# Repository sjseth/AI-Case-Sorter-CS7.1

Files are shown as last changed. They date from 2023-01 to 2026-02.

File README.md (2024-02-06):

# AI-Case-Sorter-CS7.1

This is a project for building a case sorter which uses machine vision, machine learing AI to sort cases by headstamp. This repo contains the Arduino code as well as all the 3d Models required to complete this project. 

## Instructions
Most of the information you need to build this project is available in [Instructions.pdf](Instructions.pdf).

---------
## Parts List
The parts list for this project can be found here:
[Parts List](https://www.reloadingrecipes.com/HeadstampSorter/Partslist)

--------

# CS7.1 Video Build Series

The release video for this project is here:

Watch the video (https://youtu.be/s7dy0odA44U)

Follow along with me as I build the various components of this system. 

## Classifier
Build the Classifier (https://youtu.be/lhxDmvg5AVQ)

## Sorter
Build the Sorter (https://youtu.be/rP7bBV_uqF4)

## Camera Module
Build the Camera (https://youtu.be/iOc7inAcXpQ)

## Electronics
Build the Electronics (https://youtu.be/cS54LOCpNGc)

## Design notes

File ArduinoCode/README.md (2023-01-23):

# AI-Case-Sorter-CS7.1
This repo was created to isolate all the code and resources for the CS7.1 Version

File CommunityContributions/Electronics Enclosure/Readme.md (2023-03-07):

# This is the place where you can put your Electronics Enclosure contributions to the project for cs7.1

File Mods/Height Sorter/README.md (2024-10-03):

# Height Sorter Mod

This mod is was designed by user JK and made to sort brass by height which is usefull for seperating 223 from 300 BLK or 9mm from 380, etc. 

It requires seperate arduino code (in this folder) and leverages a different classifier base design as well as a taller tension cam. 

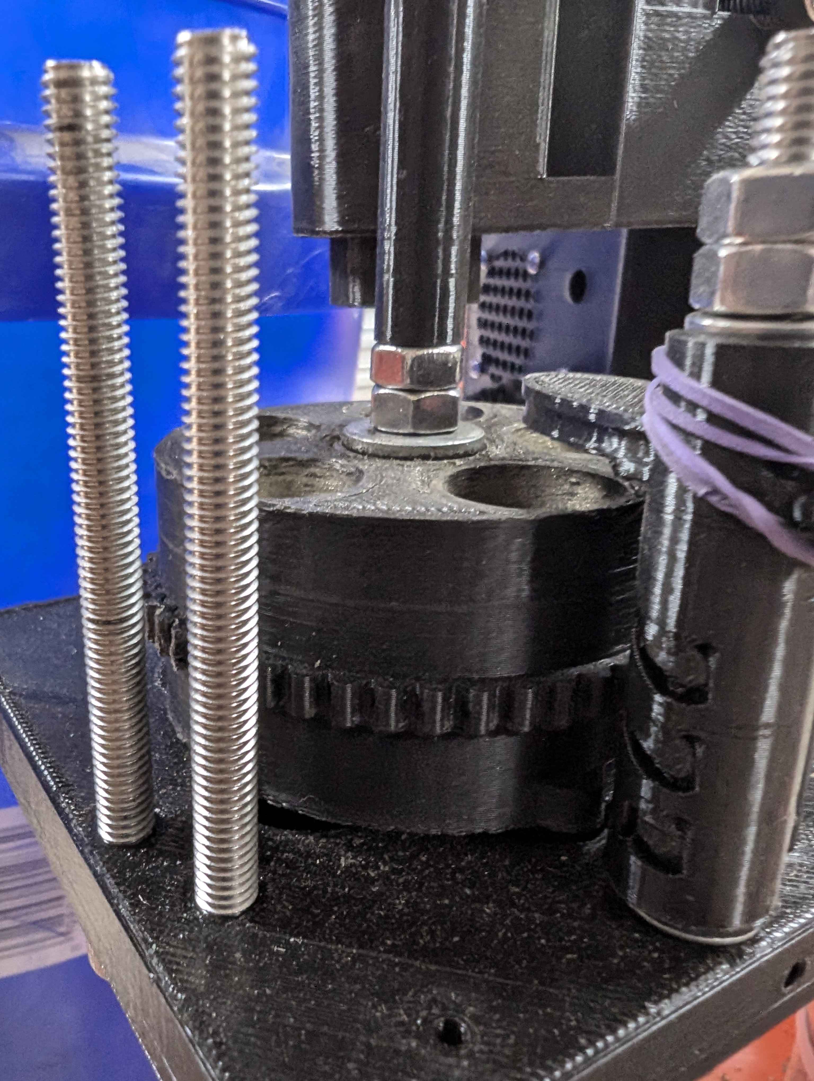
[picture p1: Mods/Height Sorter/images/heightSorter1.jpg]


<i> More details coming soon! </i>

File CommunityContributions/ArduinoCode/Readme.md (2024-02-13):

# Community Contributions for Arduino Code

### Index

* Sabre1911 - SKR PICO Support

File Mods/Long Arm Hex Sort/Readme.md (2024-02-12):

# Long Arm Hex Sort

These resources were created for those who would like to have more slots than the standard 8 provided.  By extending the arm length, we swing in a wider radius thus creating more room for buckets or containers. To make this possible, I had to change the geometry of the sort tube to have a hexagon outer contour which allows it to be printed on its side. This also has the effect of aligning the print lines with the direction the brass flows so it provides improved drop performance.

To get started, you need to print all 3 resources

[Hex Pipe Bracket](CS7.1%20-%20LAHS%20-%20Pipe%20Bracket.stl)

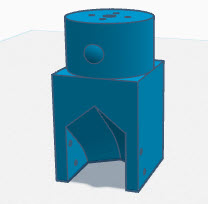
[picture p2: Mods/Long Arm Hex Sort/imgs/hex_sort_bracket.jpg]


[Hex Pipe 200mm Length](CS7.1%20-%20LAHS%20-%20HexPipe%20-%20200mm.stl)

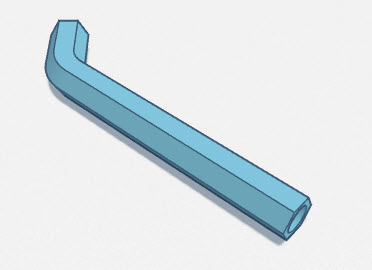
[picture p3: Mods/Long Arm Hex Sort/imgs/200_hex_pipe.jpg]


[Homing Bracket](CS7.1%20-%20LAHS%20-%20Homing%20Bracket.stl)

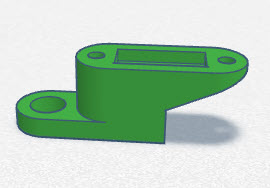
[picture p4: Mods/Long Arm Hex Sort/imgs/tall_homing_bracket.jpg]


Here is a short video of what it will look like

Video Example (https://youtu.be/aqpXGkVaJ-k)

Additionally, you will need to make some configuration updates in the AI Sorter software. 
- Set **Sort Motor Speed** to 80  (or slower)
- Set **Slot Drop Delay** to 600 (if not, the brass wont clear the tube before move)
- Set the **Slot Step Increment** to 15
- Increase the **Slot Count** to 11.

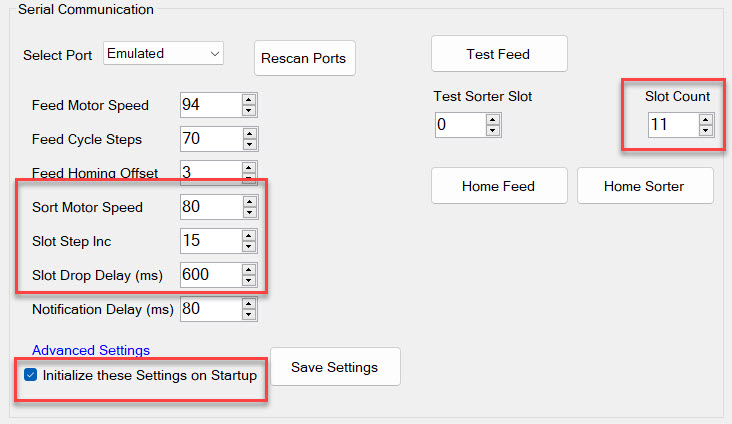
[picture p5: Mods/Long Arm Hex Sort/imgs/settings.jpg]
Settings
]

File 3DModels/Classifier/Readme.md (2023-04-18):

# Classifier Models

The parts in this folder represent everything that is needed to build the classifier. You will need to print at least one of the caliber specific feed wheels and nozzles as well. 

In the release video, there were a few add-ons which can be found in the Community Folder at the top/root folder in the repo. Those items are linked here as well:

## [Quick Change Light Shade and Locking System](https://github.com/sjseth/AI-Case-Sorter-CS7.1/tree/main/CommunityContributions/Classifier/Karl)

## [AirDrop System](https://github.com/sjseth/AI-Case-Sorter-CS7.1/tree/main/CommunityContributions/Classifier/SJSETH)

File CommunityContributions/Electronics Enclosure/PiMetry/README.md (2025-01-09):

# PiMetry

## Spacious Electronics Enclosure

Enclosure with more space for hassle free cable management with two fan slots.
The enclosure is made for the software dimmer mod, if you want to use the physical dimmer you need to modify the case or drill a hole for it.

[Pole mount from shibby](../Shibby/CS7.1a_-_Electronics_Box_Mount_1inch.stl)

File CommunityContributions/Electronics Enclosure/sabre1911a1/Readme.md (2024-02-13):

These STLs were designed to work with the BTT SKR Pico board. They will not work with the Arduino electronics.

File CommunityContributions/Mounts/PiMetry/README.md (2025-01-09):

# PiMetry

## 2020 Mounts

These mounts are intended to be used with m4 t slot nuts and bolts.
There are many 3d printable connectors for aluminum extrusions available on the usual STL / STEP file collection sites which might come in handy.

### 2020OffsetMount

Allows mounting a 2020 extrusion aside another horizontal 2020 extrusion.

### 2020OffsetTubeMount

Allows mounting a 25mm tube aside another horizontal 2020 extrusion.

### 2020TubeMount

Allows mounting a 25mm tube on top of another horizontal 2020 extrusion.

### 2020VesaMount-TwoScrew

Allows mounting a screen with two VESA bolts to a vertical 2020 extrusion.

### Electronics Enclosure Mount

Allows mounting the electronics enclosure to a vertical 2020 extrusion.

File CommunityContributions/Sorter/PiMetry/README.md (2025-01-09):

# PiMetry

## Dust Collector Hose Sorter (6 Slot)

This 6 Slot Sorter is intended for transparent and flexible PVC 50mm ID hoses with a coiled wire.
Tested with 9mm and 308 Win cases.
2 inch hoses should work as well.

Thicker or very stiff hoses are not recommended.

The hoses are connected using eg. 40 - 60 mm hose clamps
Couplers use 5x4mm round magnets (5 diameter, 4 height)

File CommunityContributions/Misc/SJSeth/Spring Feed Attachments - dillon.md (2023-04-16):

# Dillon spring feed tube adaptor

This adaptor is for a 15mm OD spring and can be attached to both ends of the spring as it fits in the dillon collator clips as well as the AI Sorter feed tubes. 

Recommend printing it with brim of at least 6 lines for better adhesion. 

[1x15x1000 Spring](https://www.aliexpress.us/item/2251832626574002.html)

This spring took about 2 weeks to get to the US and comes with two 1000mm springs Which is enough to make aproximately 6 - 8 feed tubes. 

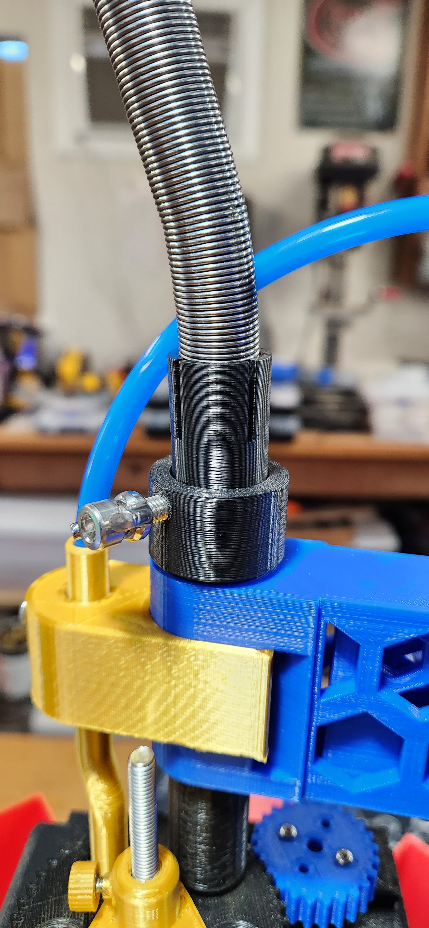
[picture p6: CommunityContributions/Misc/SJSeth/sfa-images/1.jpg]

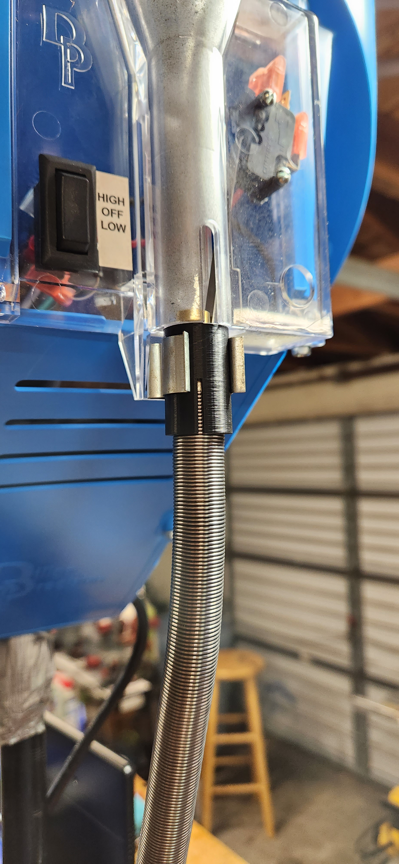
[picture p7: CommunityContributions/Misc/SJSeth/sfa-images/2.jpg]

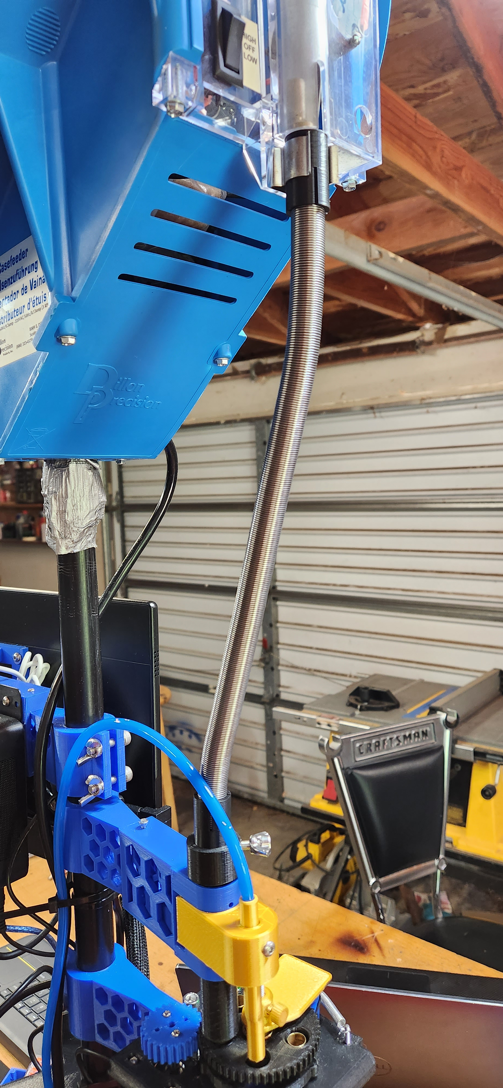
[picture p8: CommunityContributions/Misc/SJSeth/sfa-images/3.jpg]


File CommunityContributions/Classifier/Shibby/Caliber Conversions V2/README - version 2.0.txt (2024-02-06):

CS7.1 Caliber Conversions enhanced by Shibby - v2.0 - 11/20/23

Summary of changes from stock CS7.1 conversions

Conversions with "S" (i.e CS7.1s) - resized bearing hole to "19.0" and caliber designations. WARNING -Super tight fit. 
Conversions with "A" (i.e CS7.1a) - resized bearing hole to "19.2" and caliber designations. WARNING - This is a press fit. 
Conversions with "E" (i.e CS7.1e) - Stock bearing hole "19.6" just with caliber designations. Will behave as the standard CS7.1 conversions. 

Summary of changes since initial release (non version designated readme file)- 

Added "s" versions of conversions.

On the wheels, the cal designation will be on the top of the unit. Tubes have a circle sunk into them with designations popping out a touch.

Tubes are all caliber labeled with no letter designation in the naming scheme. Treat them as you would the normal files. 

Tube Varient - Keyed for BF556 feeder adaptors

45GAP conversion created for all 3 people in the world who shoot it. Use 45acp feed tubes with it. Useful for sorting 45GAP from 45ACP in one wheel. Consider interchangeable with standard 45acp wheel. 

These work for me and I make no guarantee they work for you.

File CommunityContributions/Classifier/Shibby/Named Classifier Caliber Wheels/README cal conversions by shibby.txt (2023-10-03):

CS7.1 Caliber Conversions enhanced by Shibby

Summary of changes from stock CS7.1 conversions

Conversions with "a" (i.e CS7.1a) - resized bearing hole to "19.2" and caliber designations. WARNING - This is a press fit so it may or may not work for you depending on how you have dialed in the printer you are using and the bearings you are using. 

Conversions with "E" (i.e CS7.1E) - Stock bearing hole "19.6" just with caliber designations. Will behave as the standard CS7.1 conversions. 

These work for me and I make no guarantee they work for you.

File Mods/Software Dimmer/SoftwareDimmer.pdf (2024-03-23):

# CS7.1 Software Light Dimmer Mod

### Overview

This mod replaces the hardware based light dimmer knob in the electronics box with a software-controlled system. Arduino supports PWM (pulse width modulation) signals which can be relayed through a pwm switch. In this mod, we are using the same MOSFET relay switch which is used for the AirDrop mod .

### Hardware Required

The only additional hardware required for this mod is the MOSFET pwm switch/relay which is the same one we use for the Airdrop mod.

https://amzn.to/3Ac9f7Y

### Installation

Unfortunately, not all pins are supported on the Arduino for PWM signals so we need to “trade” one of the currently used pins which supports PWM for one that doesn’t. On the Arduino Shield, pin D13 (labeled SpnDir) will become the new pin for proximity sensor (currently X+ or D9) and we will use the X+ pin for the PWM dimmer signal.

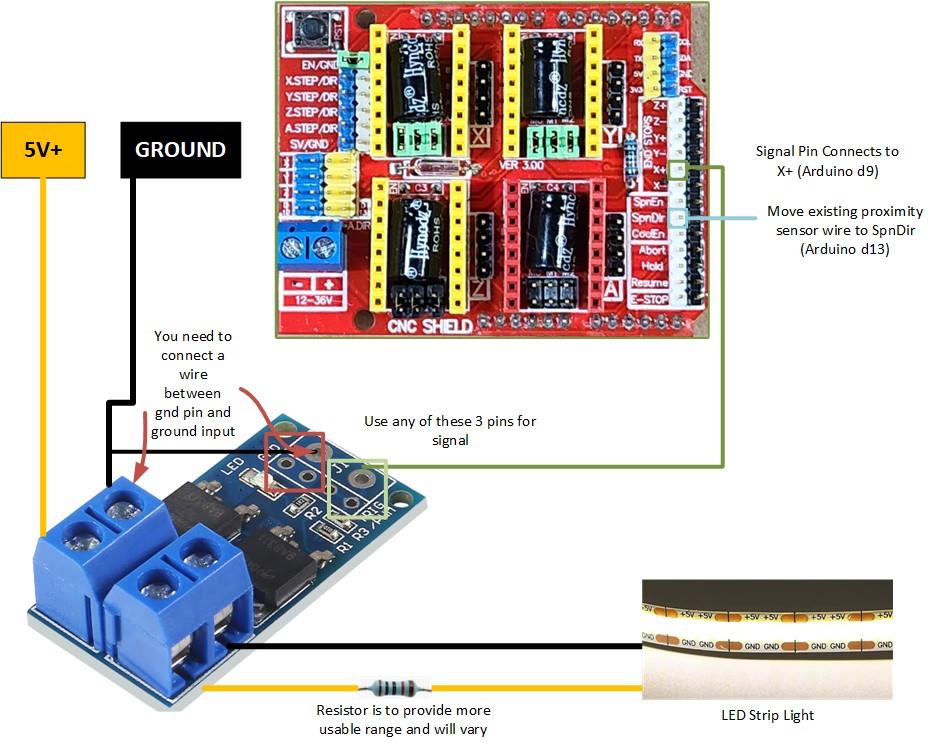
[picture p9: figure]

### Inline Resistor

The inline resistor as seen in the screenshot above is not required but can help to provide a better range of light depending on your setup. For instance, if you are using clear PLA in your light ring, you may want to add a 1k resistor. For a white PLA light ring, a value closer to 200 ohm may be more appropriate. It is recommended to try it without a resistor first and see if you are able to get the right amount of light while still having range to adjust up or down. The range of the dimmer control is 0-255.

### Configuring the Arduino

Finally, you need to make two changes in the Arduino code to enable and use this feature.

The first parameter you need to change is named UseArduinoPWMDimmer and the value needs to be set to true as seen in the screenshot below.

The second value you can change is the default light brightness value. Note that once you enable this mod, you will have an option to adjust this value in the software, so it is fine to leave the value as set.

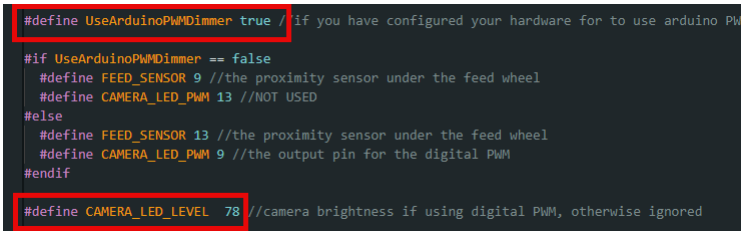
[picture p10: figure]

Once you have updated the code, you need to upload it to your Arduino. When that is complete, close the Arduino IDE and launch the software (v1.1.45 or later)

You will now see an option in the software to adjust the light brightness in the Configuration panel. It is best to hit the “Preview” button to turn on the camera and then adjust the slider until you achieve the appropriate brightness.

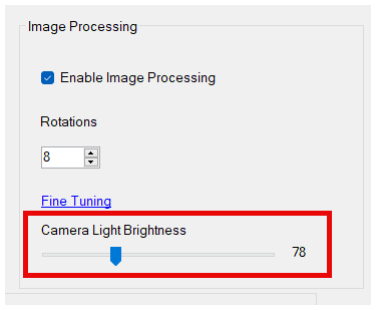
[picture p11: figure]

Be sure to save your configuration changes once you have adjusted this setting.

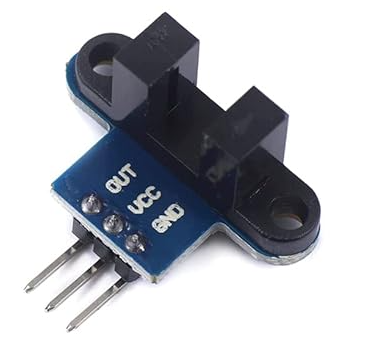
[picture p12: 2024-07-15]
CommunityContributions/Classifier/SJSETH/Optical_Homing_Sensor/imgs/sensor_amz.png

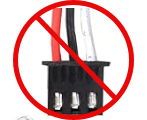
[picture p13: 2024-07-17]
CommunityContributions/Classifier/SJSETH/Optical_Homing_Sensor/imgs/sensorwire2.png

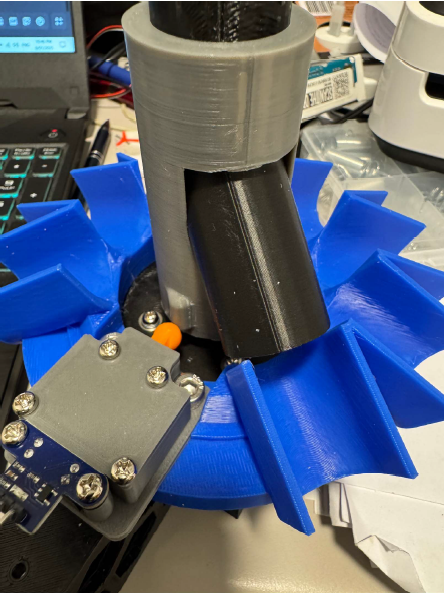
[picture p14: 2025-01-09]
CommunityContributions/Sorter/Mullet/Optical Sorter Switch/images/image.png

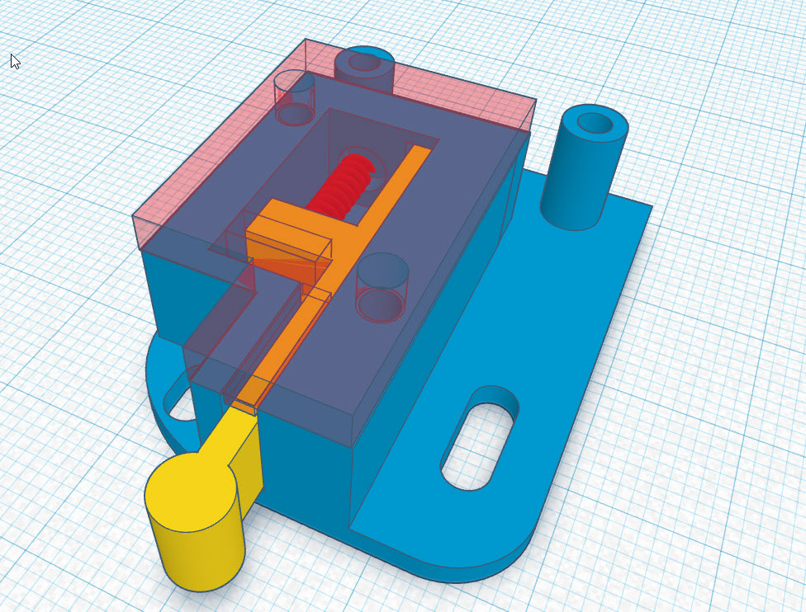
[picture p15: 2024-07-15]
CommunityContributions/Classifier/SJSETH/Optical_Homing_Sensor/imgs/sensor3d.jpg

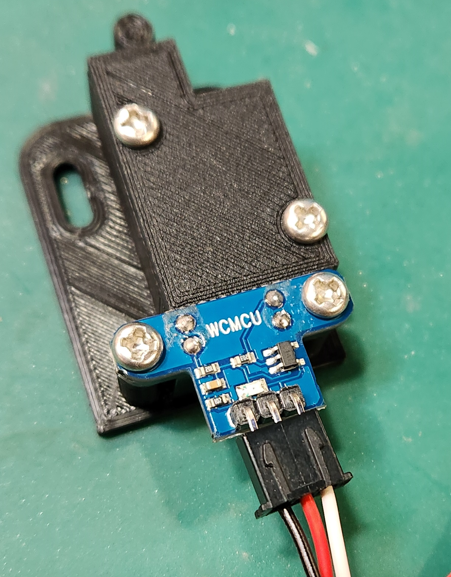
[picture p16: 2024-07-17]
CommunityContributions/Classifier/SJSETH/Optical_Homing_Sensor/imgs/sensorwire1.png

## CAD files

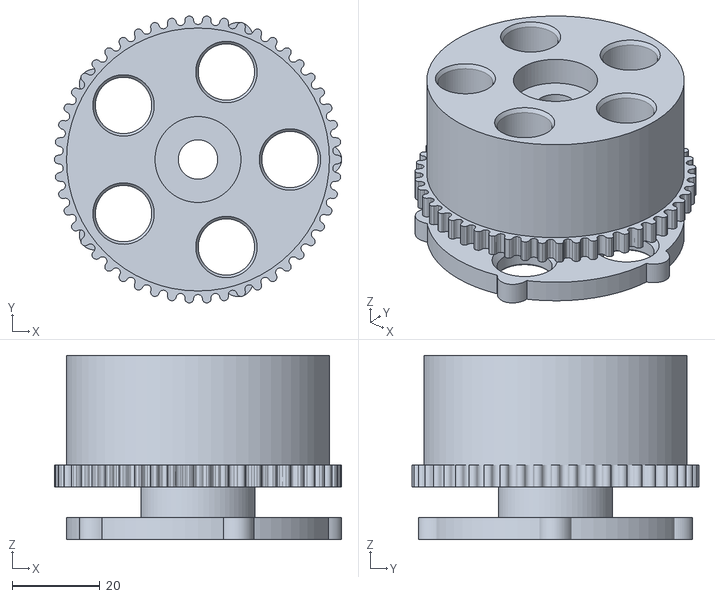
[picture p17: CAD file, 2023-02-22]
3DModels/Classifier/Caliber Specific Parts/223_556/CS7.1 223_556 Feed Wheel.stl
65.6 x 65.5 x 42.0

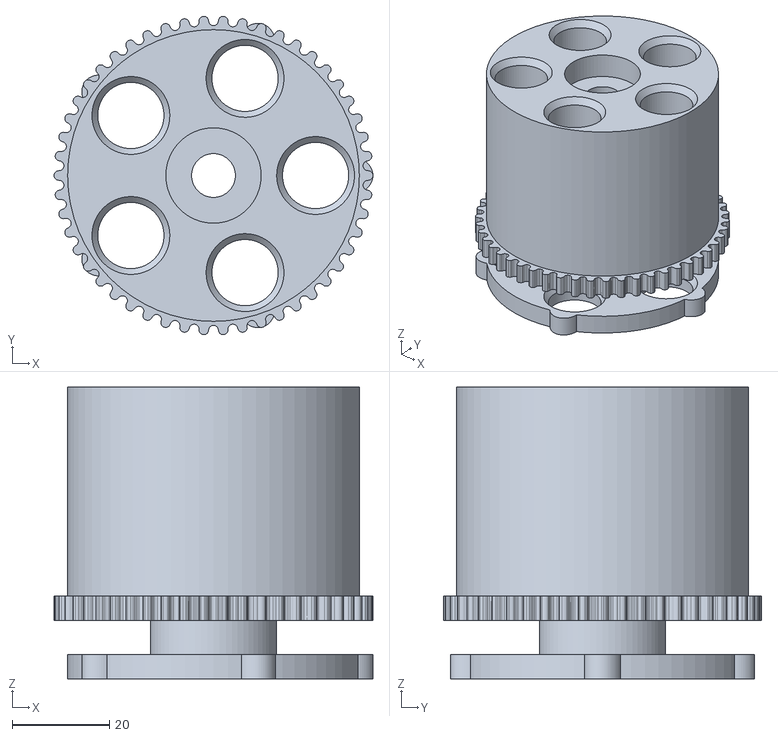
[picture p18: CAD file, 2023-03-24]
3DModels/Classifier/Caliber Specific Parts/30-06_270/CS7.1 30.06 Feed Wheel.stl
65.6 x 65.5 x 60.0

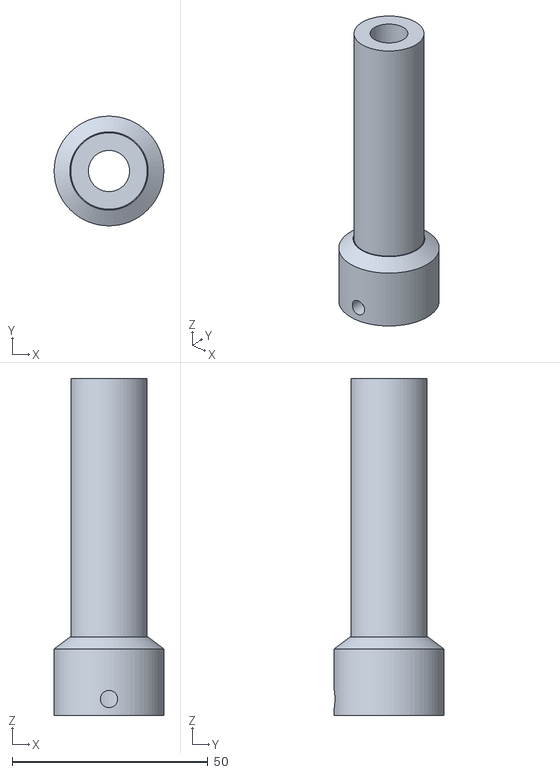
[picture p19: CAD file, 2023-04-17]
3DModels/Classifier/Caliber Specific Parts/300_Blackout/CS7.1 300 Blackout Feed Nozzle.stl
28.0 x 28.0 x 86.0

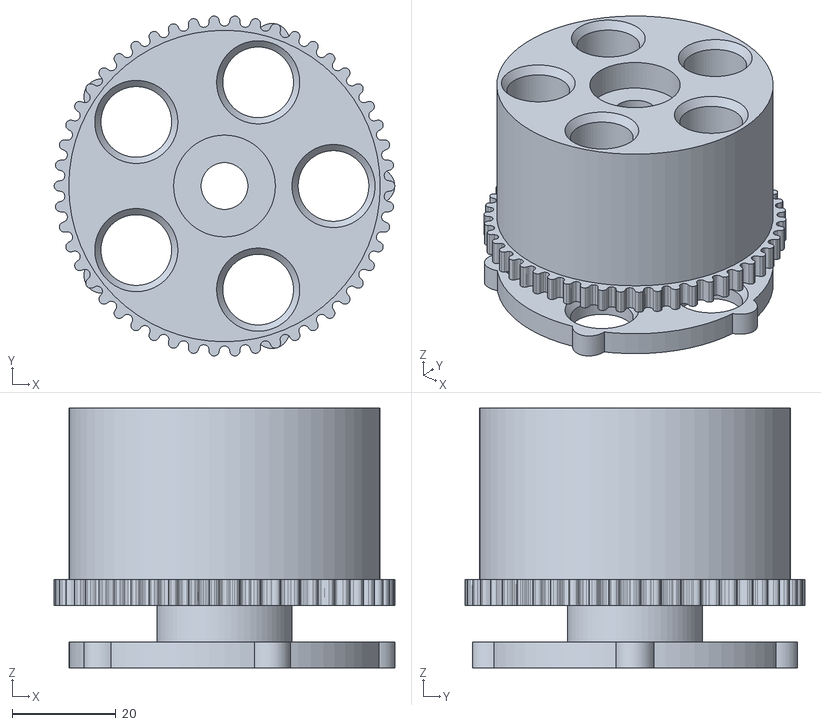
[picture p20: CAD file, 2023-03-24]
3DModels/Classifier/Caliber Specific Parts/308win/CS7.1 308Win Feed Wheel.stl
65.6 x 65.5 x 50.0

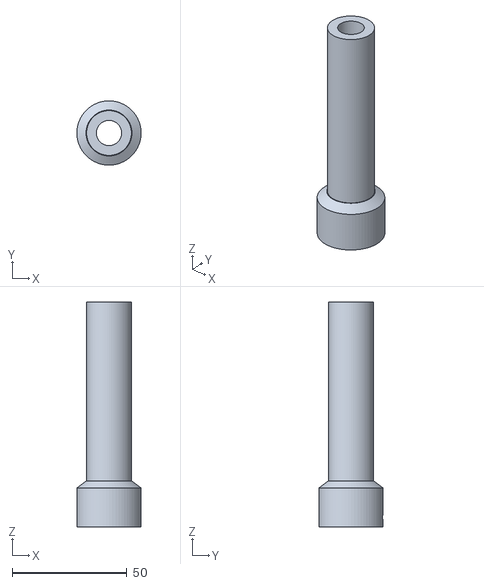
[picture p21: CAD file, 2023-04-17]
3DModels/Classifier/Caliber Specific Parts/32SWLong/CS7.1 32SWLong Feed Nozzle.stl
28.0 x 28.0 x 98.0

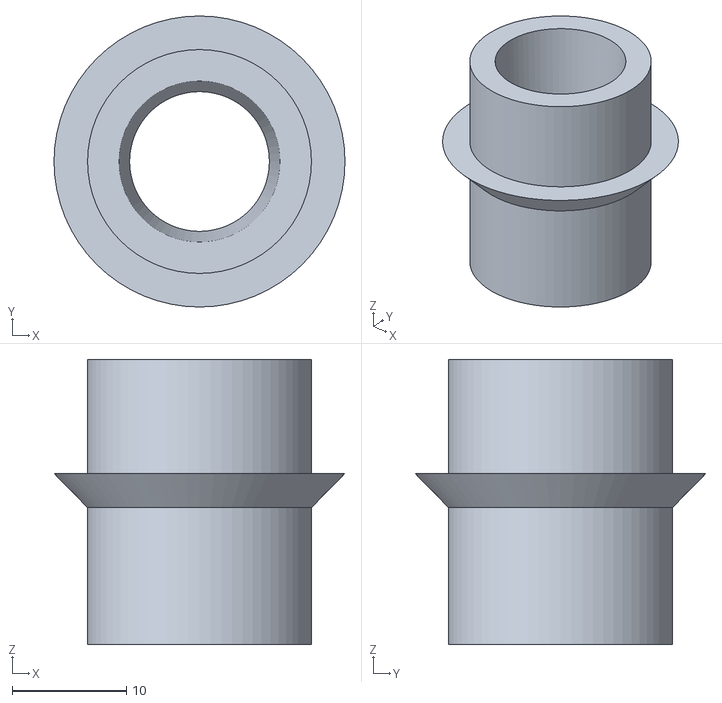
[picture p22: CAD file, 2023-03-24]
3DModels/Classifier/Caliber Specific Parts/38_Special/CS7.1 38 Special Drop Nozzle.stl
25.5 x 25.5 x 25.0

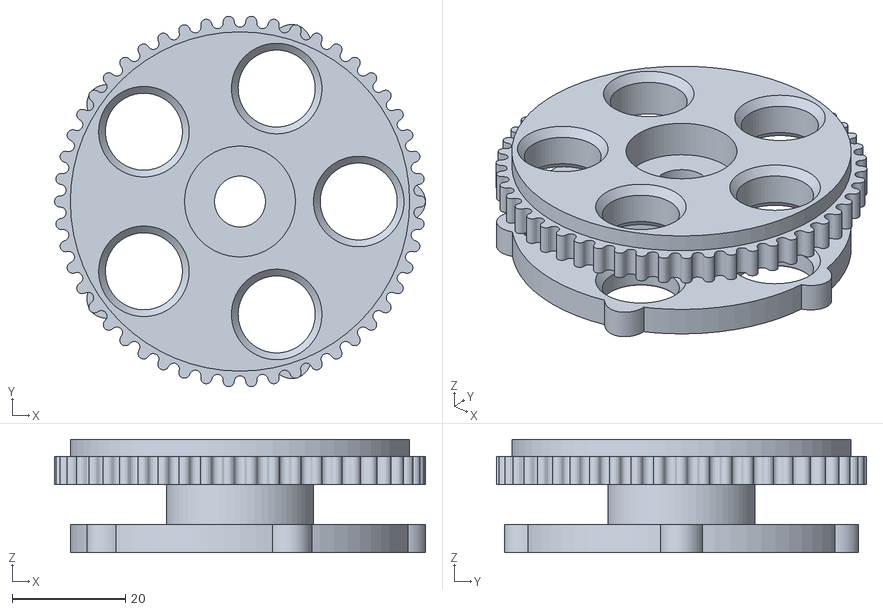
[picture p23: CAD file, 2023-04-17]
3DModels/Classifier/Caliber Specific Parts/40SW/CS7.1 40SW Feed Wheel.stl
65.6 x 65.5 x 20.0

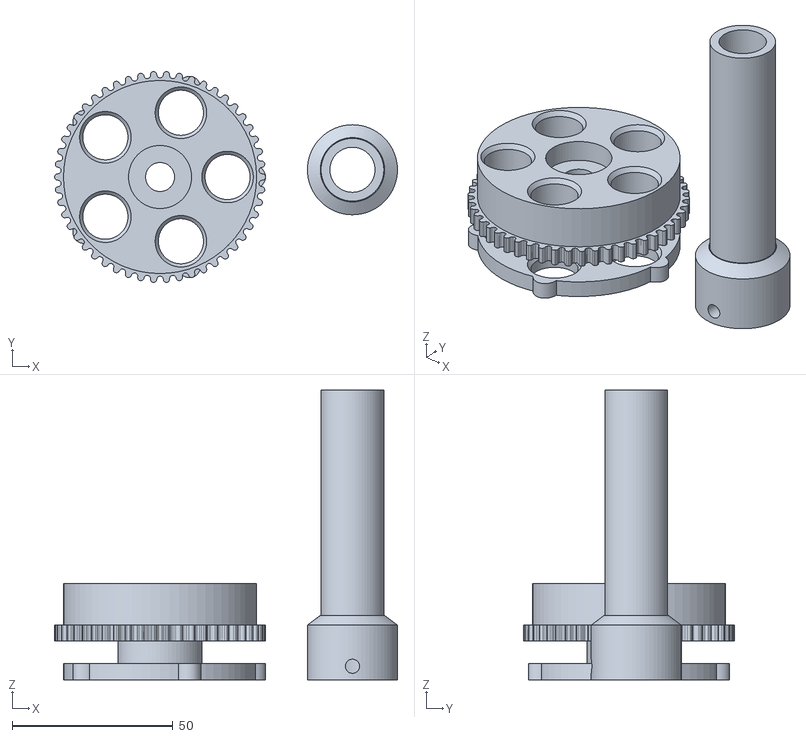
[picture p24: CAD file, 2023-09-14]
3DModels/Classifier/Caliber Specific Parts/45Colt_44Mag/CS7.1 Caliber Conversion 45Colt_44Mag.stl
106.6 x 65.5 x 90.0

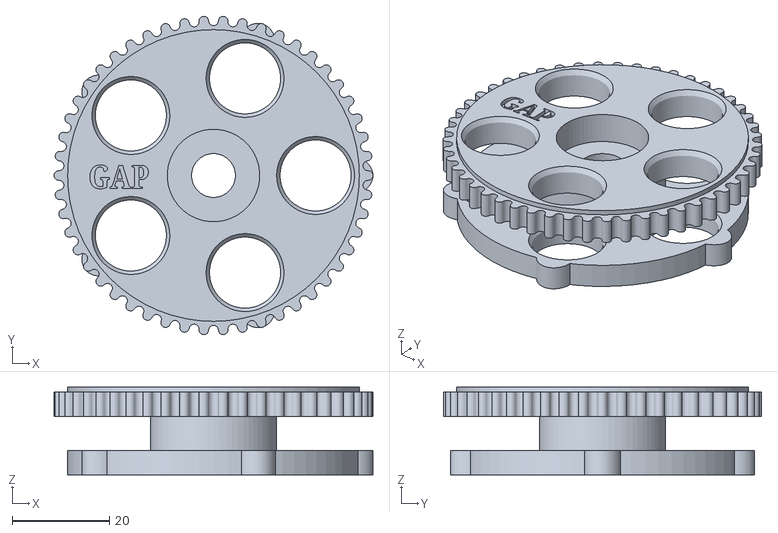
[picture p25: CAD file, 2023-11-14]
3DModels/Classifier/Caliber Specific Parts/45GAP/CS7.1e_Caliber_Conversion_45gap.stl
65.6 x 65.5 x 18.0

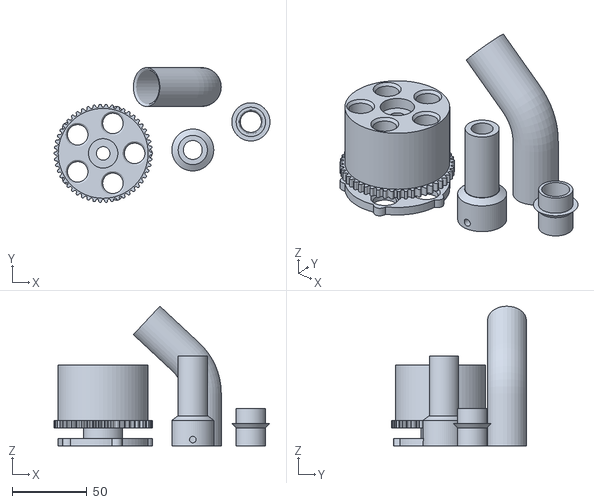
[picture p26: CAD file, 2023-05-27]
3DModels/Classifier/Caliber Specific Parts/7.92x57_Mauser/CS7.1 Caliber Conversion 7.92x57M.stl
144.1 x 90.0 x 93.2

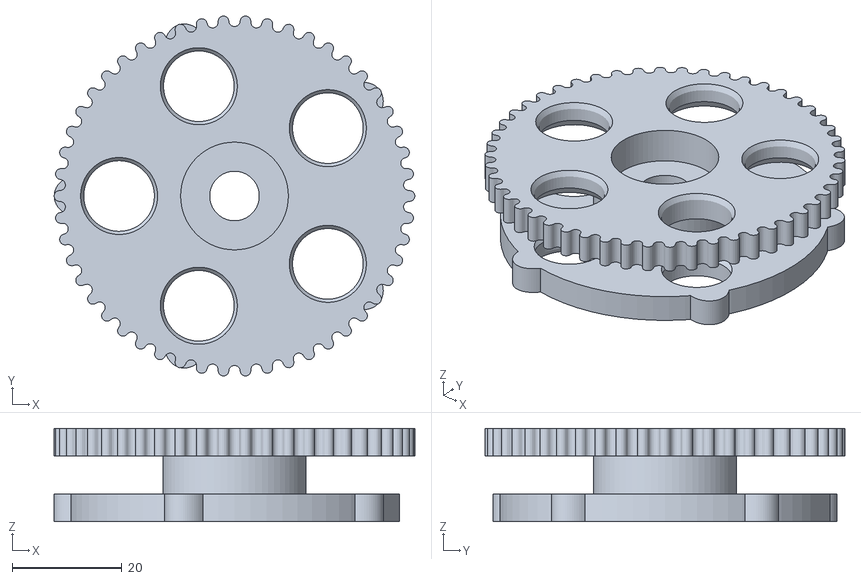
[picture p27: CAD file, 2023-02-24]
3DModels/Classifier/Caliber Specific Parts/9mm/CS7.1 9mm Feed Wheel.stl
65.6 x 65.5 x 17.0

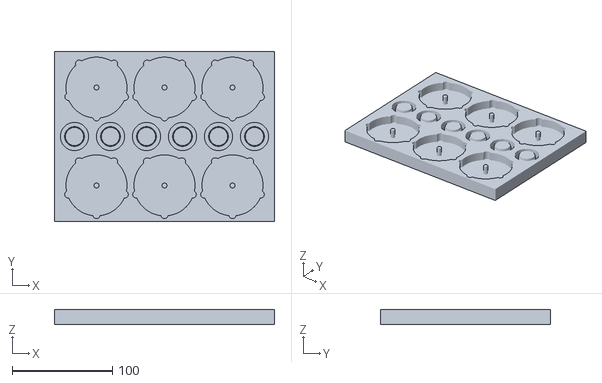
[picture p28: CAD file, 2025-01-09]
3DModels/Classifier/Caliber Specific Parts/CS7.1 Caliber Conversion Kit Tray for Shibby Drop Tubes.stl
220.0 x 170.0 x 15.0

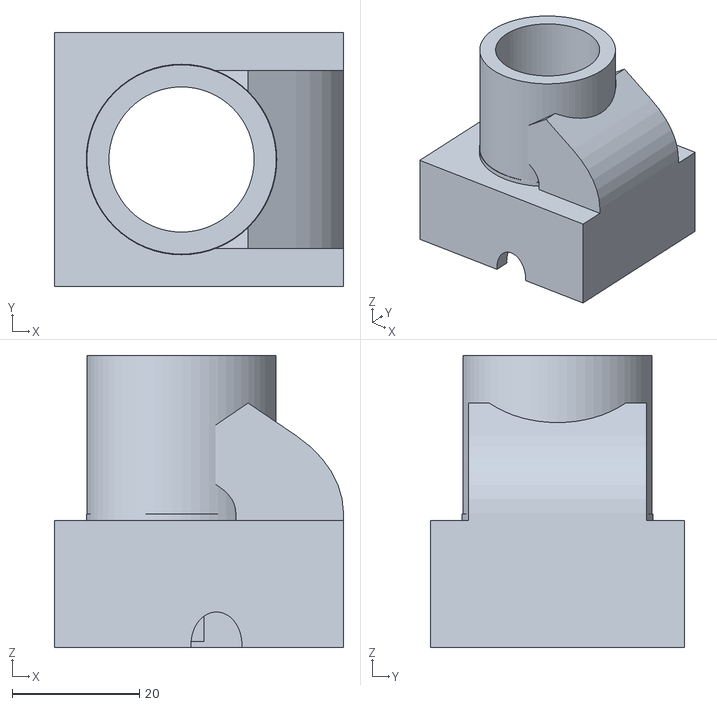
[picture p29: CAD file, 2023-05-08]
3DModels/Classifier/CameraV2/CS7.1 Camera Module V2.stl
45.5 x 40.0 x 46.0

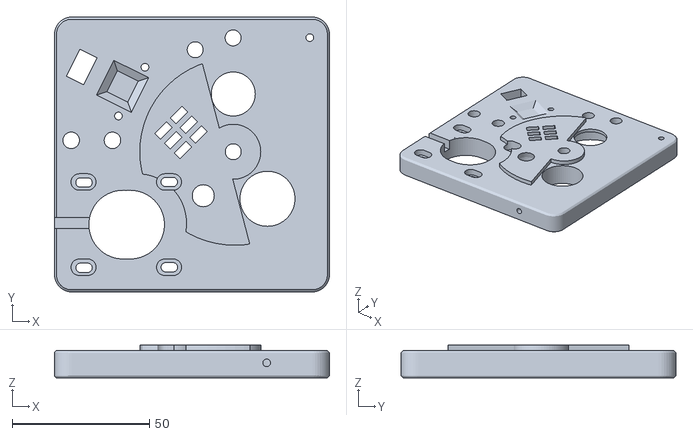
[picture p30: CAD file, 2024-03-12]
3DModels/Classifier/CS7.1 Classifier Base v2.1.stl
100.0 x 100.0 x 12.0

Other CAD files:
3DModels/Classifier/Caliber Specific Parts/45Auto/CS7.1 45Auto Drop Nozzle.stl
3DModels/Electronics Enclosure/CS7.1 Electronics Box Mount.stl
3DModels/Mounts/3_4in_Schedule30/CS7.1 Pole Mount - .75s40 - SOLID.stl
3DModels/Mounts/CS7.1 Pole Mount - 1in - SOLID.stl
3DModels/Classifier/CS7.1 Camera Light Ring.stl
3DModels/Classifier/CS7.1 Camera Module.stl
3DModels/Classifier/CS7.1 Classifier Base v2.stl
3DModels/Classifier/CS7.1 Classifier Base.stl
3DModels/Classifier/CS7.1 Classifier Drive Gear.stl
3DModels/Classifier/CS7.1 Classifier Drop Nozzle - Universal.stl
3DModels/Classifier/CS7.1 Classifier Feed Bracket.stl
3DModels/Classifier/CS7.1 Classifier Feed Nozzle Adapter Nut.stl
3DModels/Classifier/CS7.1 Classifier Feed Nozzle Adapter.stl
3DModels/Classifier/CS7.1 Classifier Light Shade.stl
3DModels/Classifier/CS7.1 Classifier Mount_1in_26mm.stl
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

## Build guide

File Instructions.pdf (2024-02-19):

# CS7.1 Instructions Manual and Build Guide

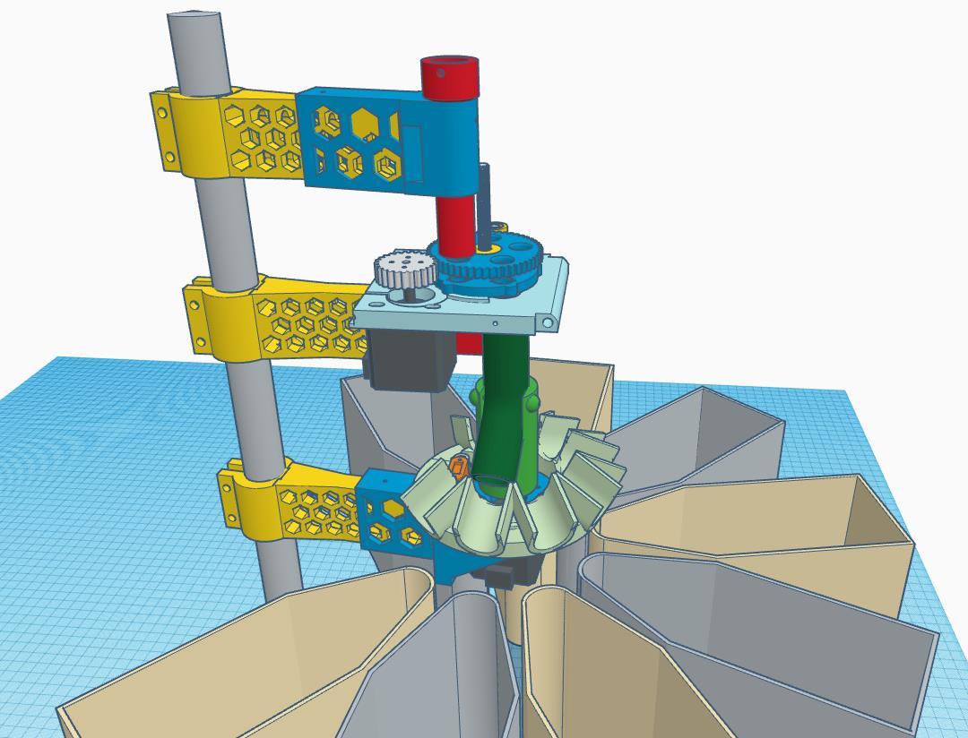
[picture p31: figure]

Introduction

5

Computer Requirements

5

Overview

5

Building the Classifier

6

Printing the Classifier Models

– General Settings

6

Classifier Printable Parts Listing Diagram

7

Classifier

– Base Plate

7

Classifier

– Camera Module

7

Classifier

– Camera Light Ring

7

Classifier

– Feed Wheel (Caliber Specific)

8

Classifier

– Drive Gear

8

Classifier

– Feed Bracket

8

Classifier

– Light Shade

8

Pole Mount

8

Classifier

– Feed Nozzle (Caliber Specific)

8

Classifier

– Tension Cam

8

Classifier

– Tension Cam Shim

8

Classifier

– Drop Nozzle (Caliber Specific)

8

Classifier Assembly

9

Assembly Diagram

9

Assembly Steps

9

Camera Assembly | 10
Focusing the Camera | 11
Build the Light Ring | 11
Building the Sorter | 13

Printing the Sorter Models

– General Settings | 13
Sorter Printable Parts List Diagram | 14

Sorter

– Base & Pole Mount | 14

Sorter

– Base 8 Slot Ramp | 14

Sorter

– Pipe Bracket | 14

Sorter

– Sort Pipe | 14

Sorter

– Homing Bracket | 15

Sorter – Sort Bin | 15
Sorter Assembly | 15
Ensure Sorter / Pole Mount fitting are snug | 15
Install the Motor | 15
Install the Flange | 15
Connecting the Sorter Pipe Bracket to Motor | 15
Install the Sorter Base 8 Slot Ramp | 15
Install the Homing Sensor and Bracket | 16
Install the Sorter Pipe | 16
Pole Mount | 16
Electronics and Enclosure Assembly | 16
Printing the Enclosure Models – General Settings | 16
Enclosure – Box | 16
Enclosure – Lid | 16
Electronics Assembly | 16
QUICK STEPS | 17
Detailed Instructions | 17
Create or designate a 12v Rail | 17
Create a 5v Rail | 17
Create a ground rail | 17
Install 40mm Fan | 17
Install LED Dimmer | 18
Install Power Jack (12v) | 18
Install Power Switch | 18
Install the Arduino Uno | 18
Install the CNC Motor Shield | 18
Install Jumpers | 19
Install the TMC2209 Motor Controllers | 19
Connect power wires and ground | 19
Feed Homing Sensor | 19
Sorter Homing Sensor | 19
Feed Sensor (Proximity Sensor) | 19
Attach Motor Cables | 19
Optional 5v Power | 19

Configuring vRef (reference voltage) on TCM2209 | 20
Uploading Code to the Arduino | 22
Download and Install Arduino IDE | 22
Download the CS7.1 sorter Arduino Code | 22
Connect the Arduino to your computer via USB cable. | 22
Upload the code(firmware) to the Arduino microcontroller | 23
How to modify code for testing without sensors connected | 23
Testing the Sorter in Serial Monitor Console | 23
List of Serial Monitor Commands | 24
Parts List | 25
Troubleshooting | 25
Motors not running smoothly or correctly. | 25
Motors running backwards. | 25

## Introduction

This document is a guide for those who are interested in creating an AI Headstamp Sorter machine. This document references resources found in the GitHub Repository at https://github.com/sjseth/AI-Case-Sorter-CS7.1

Also available is the video build series at:

Release Video: https://youtu.be/s7dy0odA44U
Classifier Assembly - https://youtu.be/lhxDmvg5AVQ Electronics - https://youtu.be/cS54LOCpNGc Sorter Assembly - https://youtu.be/rP7bBV_uqF4
Camera Module - https://youtu.be/iOc7inAcXpQ

### Computer Requirements

Central to this project is the Windows based software which handles the picture classification and builds the machine learning models used for classification. Here is the list of requirements to run the software:

- Windows 10 (x64) or greater
- 64bit processor architecture
- 16GB Ram (recommended)
- Processor must support AVX instructions (AVX, AVX2, etc). Most processors made after 2015 support it. Most Celeron and Atom processors do not support AVX instructions.
- C++ VS Redistributable
- (2) USB 3.0 or type A ports. (a USB hub can be used if the machine has other USB port types)

### Overview

The AI Headstamp Sorter machine has 3 major components:

- Classifier – The part of the machine which takes a picture of the brass and classifies it. Then it is dropped into the sorter. The camera assembly is included as part of the classifier.
- Sorter – The bottom half of the machine which has a rotary arm with tubes to sort the brass into bins.
- Electronics & Enclosure – The electronics are housed in an enclosure which is powered by an external power supply and connects to the computer using USB.

All of the 3D Models are code are available in the GitHub repo and while it is possible to download individual files, because the repo is less than 20MB, it is recommended to download the entire repo so that you have all the files available for print and reference. You can download the entire repo from the repo home page by clicking the code menu and selecting download Zip. Once you have downloaded the zip, you should extract it to a known location (Documents or Desktop) so that you will have easy access/reference.

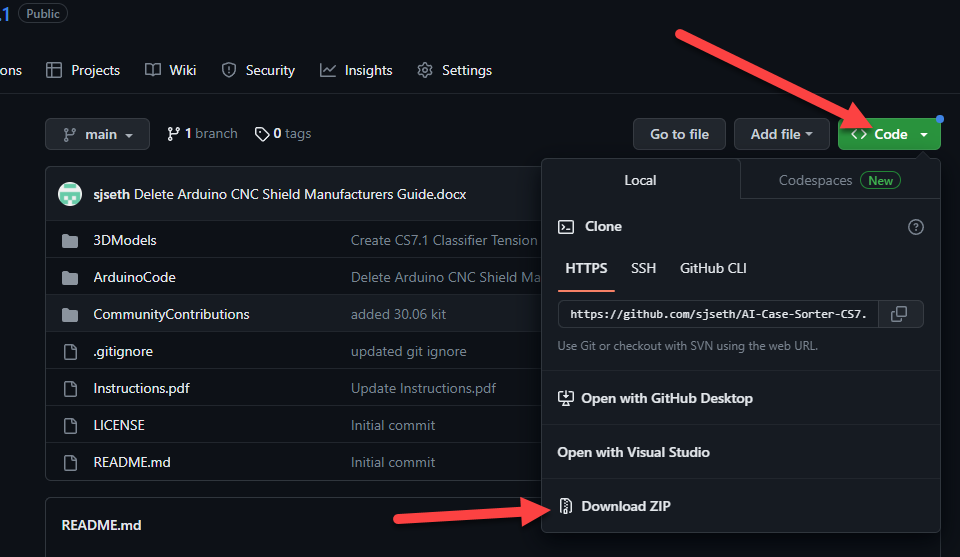
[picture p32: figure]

## Building the Classifier

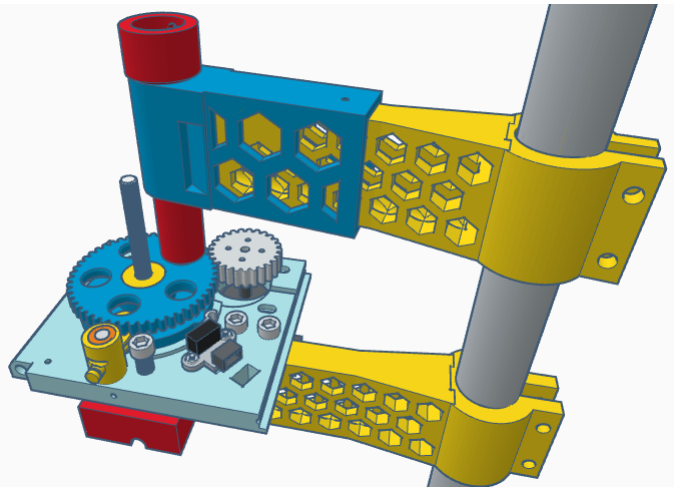
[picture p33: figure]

### Printing the Classifier Models – General Settings

It is highly recommended that you use Black PLA+ for all components in this project. I have used the JAYO brand of PLA+ with great success. For all models, these are the general print settings that I have used:

- Nozzle Temp: 222C
- Bed Temp: 60C
- Layer Height: .20mm
- Support overhang angle: 88 degrees.
- Support type: tree
- Infill: 30%
- Infill Pattern: Lines or Grid

These should be the assumed print settings for all models unless specific changes/overrides are indicated below.

The models account for shrinkage already and though a calibrated printer will give you better dimensional results, if you print all the parts with the same print settings, everything should fit together with minimal post-print modification.

The classifier models are available in the GitHub repo folder 3dModels/Classifier (https://github.com/sjseth/AI-Case-Sorter-CS7.1/tree/main/3DModels/Classifier)

Classifier Printable Parts Listing Diagram

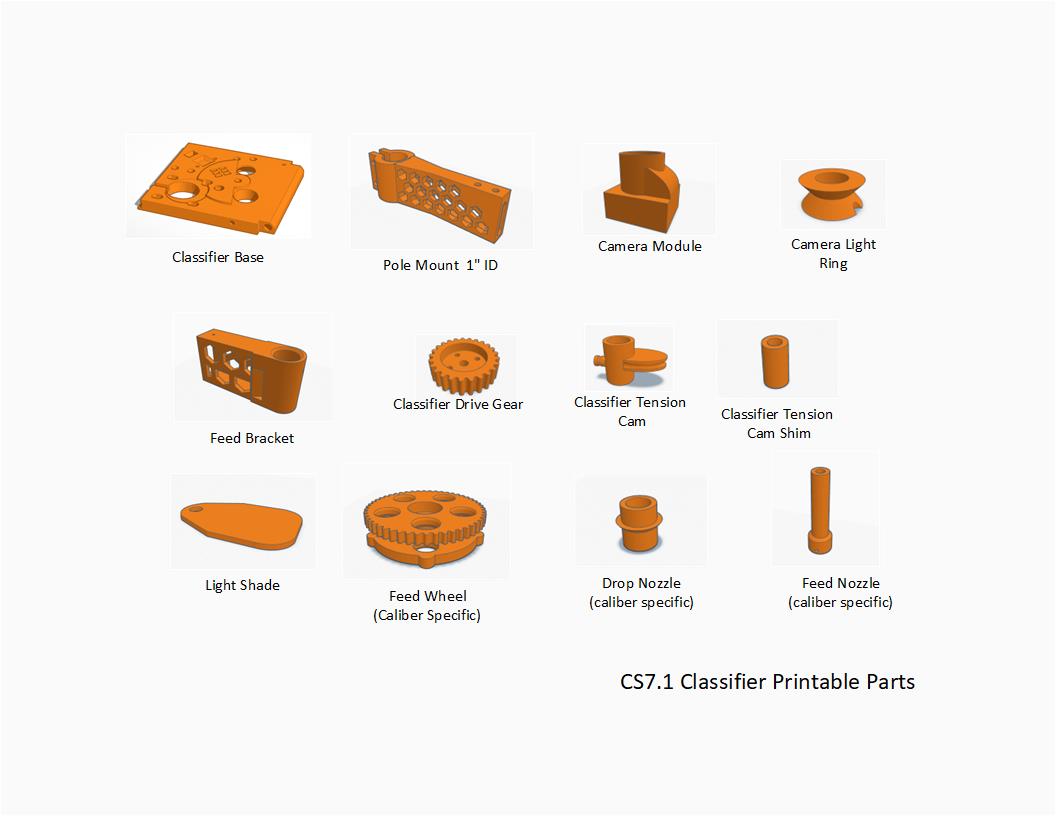
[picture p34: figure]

Classifier – Base Plate
Recommend using black PLA+ but if you decide to use a different color, you will need to “black-out” the bottom of the camera hole and surrounding side surfaces to keep the picture dark. Flat black paint or a sharpy will usually work as these parts do not have any wear.

Classifier – Camera Module
Layer Height: .16mm (or smaller).

The camera module has some very small screw holes to facilitate the m2 screws needed to bolt on the blower fan. The more precision you can get out of your printer, the better. Recommended to use Black PLA or PLA+ as any other color will result in less-than-optimal image processing results.

It may also help to slow down your print speed on the first 10 layers of this print to get better screw hole definition.

Classifier – Camera Light Ring
Color Material: Non-Opaque White PLA.

The purpose of this part is to diffuse the light from the LED light strip. The more translucent the material, the better. Generally cheap white PLA works great here.

Classifier – Feed Wheel (Caliber Specific)
This wheel can be printed in either orientation however, it is recommended to print the wheel with the bottom (non-geared side) down. If you are printing to a smooth glass bed, this may result in a very shiny bottom on the part and you will need to “scuff” it with some light sandpaper (300-400 grit) to avoid reflections from the camera backlight. Using print base with a matte texture is recommended. (Example of magnetic print surface). (https://www.amazon.com/Creality-Original-Flexible-Removable-235X235MM/dp/B07X3WBNPX) You may get better results using tree supports if your slicer supports them.

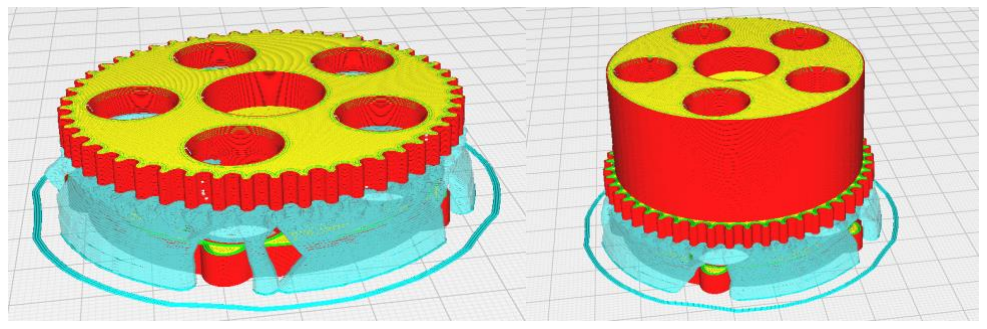
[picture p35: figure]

Classifier – Drive Gear
This part can be printed in any color you choose. Recommend PLA+ for greater durability but no problems have been reported with just standard PLA.

Classifier – Feed Bracket
This holds the feed nozzle and can be adjusted so that the tip of the nozzle hovers approx. 2-3mm over the feed wheel. The bracket attaches to the 2nd pole mount.

Classifier – Light Shade
The light shade is attached to the M6 feed wheel axel via a nut and should hover over the camera hole just above the feed wheel about 5mm. Should be printed in black or similar dark filament.

Pole Mount
You will need to print 3 pole mounts in total. Two for the classifier and 1 for the sorter. This can be any color but recommended to use PLA+ for increased strength.

Classifier – Feed Nozzle (Caliber Specific)
Any desired color can be used for this part.

Classifier – Tension Cam
- Layer Height: .16
- Infill: 100%

Classifier – Tension Cam Shim
This part should thread snugly onto an M6 bolt or threaded rod. It should also fit loosely in the tension cam. Print the part as is and if there is a fit issue, scale the part up or down by 1% until you get the desired fit. The cam should move freely and easily when installed over this part.

This part should be printed in Black.

Classifier – Drop Nozzle (Caliber Specific)
The drop nozzle is designed cancel the rotational effect on the falling brass and allow the brass to drop straight down into the sorter tube which as the effect of a smoother/faster sort drop (vs the brass rattling around in the tube and not making it into the desired sorting bucket in time. Standard print settings apply but the part should be a press fit into the drop hole. If it is too tight/loose, use scaling in your slicer to upscale/downscale by 1%.

This part is not required but may improve performance. It can be printed in the color of your choosing.

### Classifier Assembly

Assembly Diagram

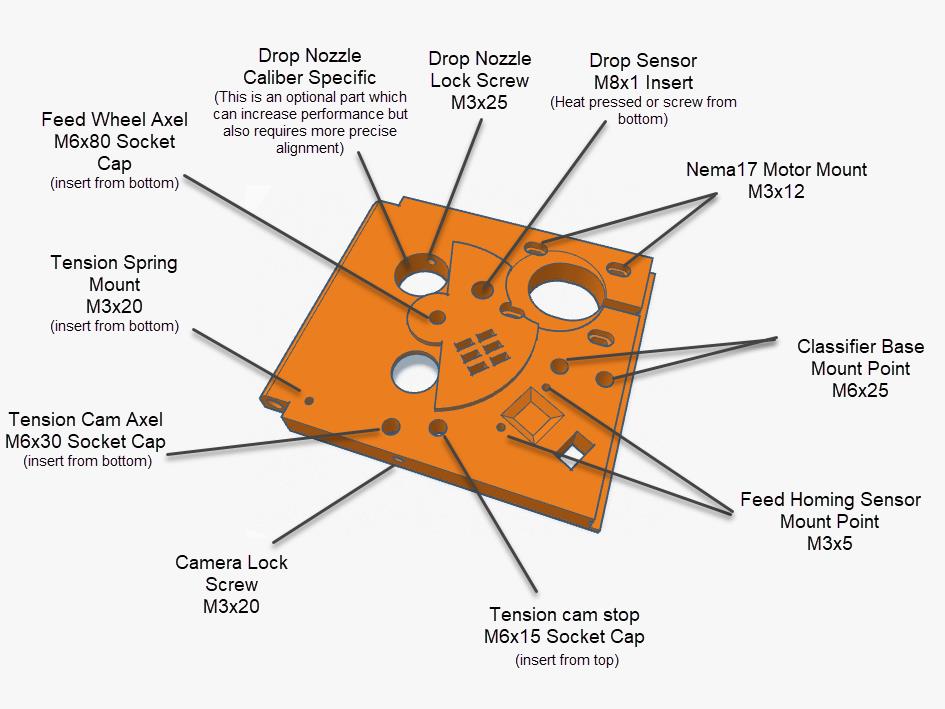
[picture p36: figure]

Assembly Steps
Installing the parts in the correct order can save you time and frustration. Here is the best order I have found for construction:
1. Test fit the camera housing into the base. It should have a snug press fit. If the fitment is loose, you will need to use the Camera Lock Screw (m3x20) to secure the camera in place. You will need to remove any burrs and might need to lightly sand the outside of the camera housing to get a good fit. We will install this part last, but it is easiest to make sure it is going to fit before installing the rest of the hardware.
2. Install the Drop Sensor insert. This is an M8x1.0 threaded insert (see parts list) (don’t confuse it with M8x1.25 which is more commonly available). The threaded insert can be threaded into the sensor hole from the bottom if you have an m8x1 bolt handy, otherwise it is recommended to use a hot soldering iron to press fit it into the hole.
Be careful not to seat the insert all the way in flush to the body and it should hang approx. 1/8in below the base.
3. Install the Proximity Sensor (Drop Sensor) into the threaded insert. You should screw this in until the top of the insert is flush or slightly below the top surface of the classifier base. If sensor is too high, it will catch on the feed wheel.

4. Install the Feed Wheel Axel (m6x80mm socket cap screw). This screw threads from the bottom and should be threaded snug to the base. DO NOT OVER TIGHTEN. If you use a different type of screw, it is possible the head of that screw may be too large and interfere with the camera hole. Socket head is recommended.
5. Install the Nema17 Motor. Do not tighten the motor screws all the way down yet. Slide the motor towards the back of the slot. Install the coupler flange on to the motor shaft.
6. Press fit the drop nozzle for your desired caliber (see caliber conversion kits). If the fit is too loose, you will need to use an m3x30 set screw to hold it in place.
7. Install Tension Cam Axel Screw from bottom and seat flush to base (M6x30). Thread the Tension Cam shim onto the tension cam screw until it is snug to the base. You should be able to thread this part by hand. If it is too tight, you might consider printing another which is 1-2% larger.
8. Install the Tension Cam spring mount from the bottom (m3x20)
9. Install the Tension Cam stop screw from the top and thread until the bolt is flush with the bottom of the base (m6x15). Slide the tension cam stop shim over the cap of the screw.
10. Insert [16x1.5 – 17x2.4] O-ring on the tension cam
11. Slide Tension cam over the tension cam shim/axel.
12. Attach extension spring to cam and spring mount. Thread m3 nut down onto spring mount screw.
Pro Tip: Rather than use a nut to secure the spring, use the edge of a sharp file or Dremel to cut a notch about 1/4in down on the m3 screw. It only needs to be deep enough to keep the spring from sliding off. This makes removal of the cam much easier.
13. Install Feed wheel with bearing preinstalled. The wheel should easily slide down over the m6 axel screw. Add a lock nut or two standard nuts to the top of the wheel. Do not over tighten as the wheel should move freely.
14. Install the homing sensor. This takes two m3x10 (or shorter) screws.

Camera Assembly
*Note. If you are using the V2 Camera, you will need to skip this part and reference the Camera Assembly V2.pdf (https://github.com/sjseth/AI-Case-Sorter-CS7.1/tree/main/3DModels/Classifier/CameraV2/Camera%20Assembly%20V2.pdf) guide.

The following diagram illustrates the parts required to complete this part of the build.

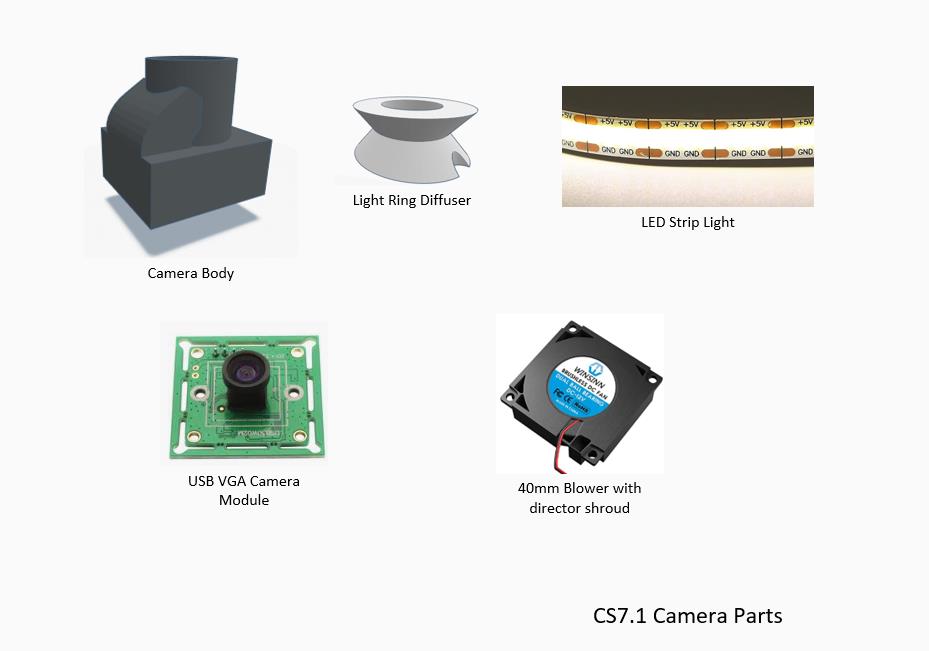
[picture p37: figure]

Here is an overview of the basic assembly steps to complete the camera module

1. Focus the camera
2. Build the Lighting Ring
3. Install the lighting ring and wiring

4. Install the camera
5. Install the Fan
6. Test

Focusing the Camera
Connect Camera USB cable and connect to a computer and open the default windows camera app. Select the VGA camera.

Set the focus of the camera by using the camera body as a guide. You can rotate the camera lens to focus the camera. Set the camera body on its side and set or hold a piece of brass approx. 4mm from the top edge of the body. Place the camera into the body and check the focus on your computer.

Once you have the camera reasonably focused, you can unplug it and set it to the side.

Build the Light Ring

1. Unroll the USB strip light and cut a section length of 5 sections using scissors or a box cutter.

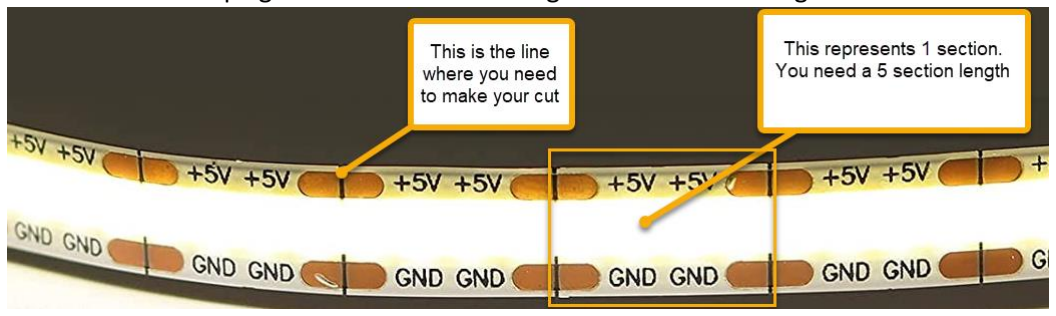
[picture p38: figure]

2. Solder a wire pair to the 5v and ground tabs. The wires should be at least 5 inches long. Recommend using yellow and black wire so the wiring is not confused later with the fan wiring but of course any color will work.
3. Wrap the light strip around the light wring with the strip facing into the ring. Make sure to align your wires with the notch in the light ring. Tightly wrap at least 2 lengths of electrical tape around the outside edge of the ring to secure the led strip and wiring in place.
4. Install the light ring into the camera housing through the top. Guide the wire pair through the offset hole (not the big center hole)

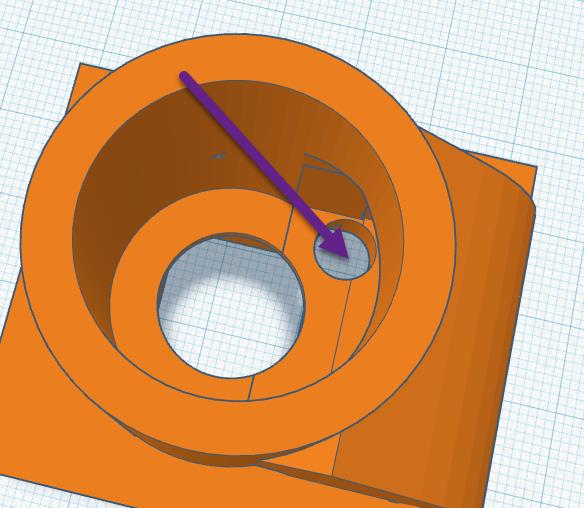
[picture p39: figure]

5. Run the wiring in the slots provided

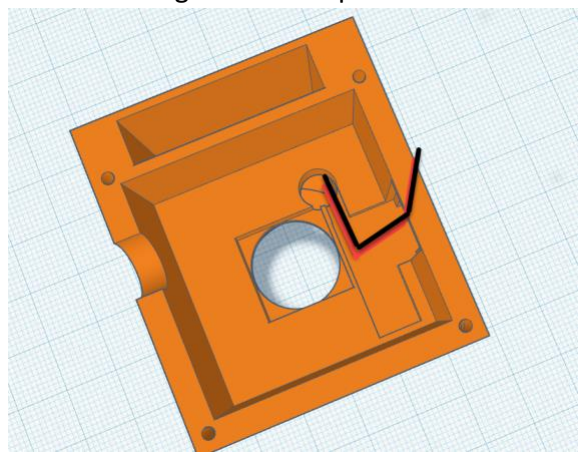
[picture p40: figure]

6. Place the camera into the house making sure the connector side is oriented with the recessed slots
7. Place a piece of foam rubber or packing foam on the back of the camera so that it is pressed firmly in the housing when the fan is installed
8. Connect the USB cable to the camera
9. Run both the USB wire and the light ring wire out the half-circle hole
10. Install the fan on top the camera housing using 2mm socket head screws. Make sure the director shroud is oriented correctly.
11. At this point all the wires should close together (fan, light-ring and camera). It may be helpful to put a piece of electrical tape around them to keep them together.
12. Install male Dupont connectors on the fan and light ring wires so they can be easily detached later.

This completes the assembly of the ring. You can test the light ring by applying 5v power to it. The fan requires 12v.

## Building the Sorter

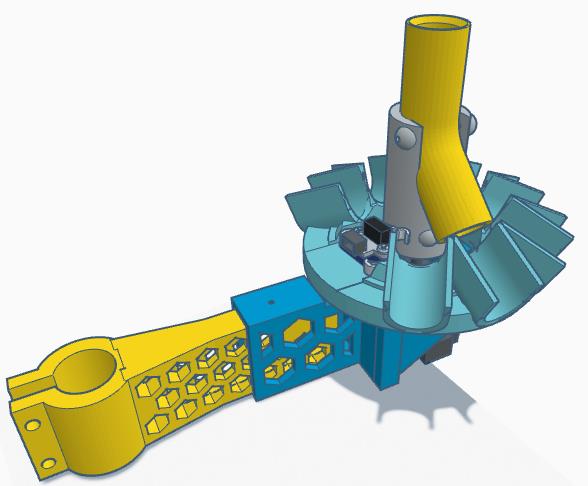
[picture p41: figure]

### Printing the Sorter Models – General Settings

When printing the sorter parts, you can use the filament type and color of your preference.

Recommend PLA+, PETG, PLA with layer height of .2.

The models account for shrinkage already and though a calibrated printer will give you better dimensional results, if you print all the parts with the same print settings, everything should fit together with minimal post-print modification.

Sorter Printable Parts List Diagram

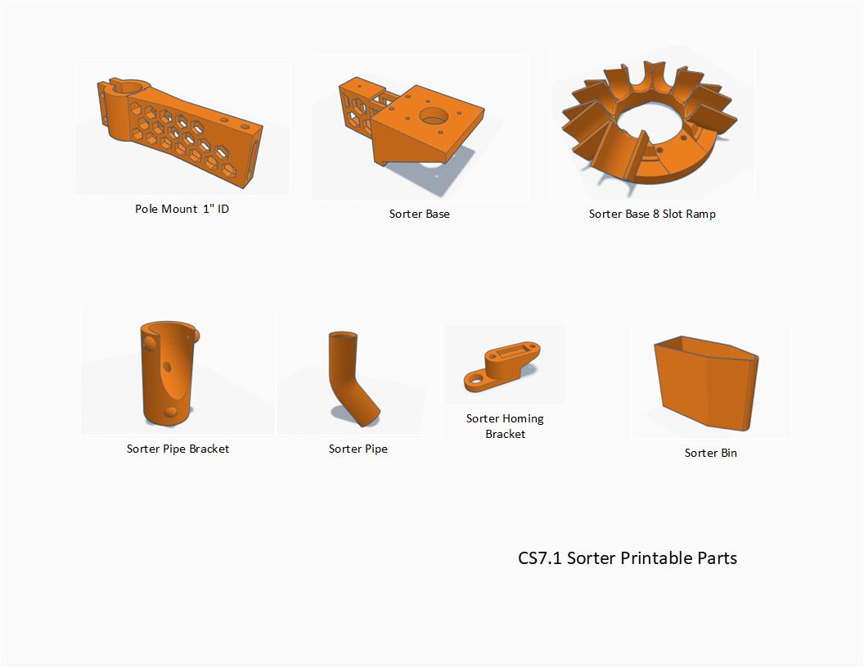
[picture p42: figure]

Sorter – Base & Pole Mount
This part can be printed in any color you choose. Recommend PLA+ for greater durability but no problems have been reported with just standard PLA. The base should be printed with standard supports with minimal support angle of 88 degrees. The base slides over the pole mount so it is highly recommended to print these two parts together with the same material. If you print these with different colors/materials, you might have to do some light sanding on the pole mount to achieve the desired fit as difference filaments often have different shrink profiles.

Sorter – Base 8 Slot Ramp
This part slips over the sorter base and is secured by two m6 screws. No specific recommendations for this part.

Sorter – Pipe Bracket
This part is attaches to the sorter motor via a 5mm coupling flange. Supports should be turned off when printing this part and it is recommended to use the minimal infill possible 5-10% max. The lighter this part is, the better as it can affect the amount of torque needed to start/stop the sorter in correct position.

Sorter – Sort Pipe
There is some benefit in printing this part as high-quality as possible. Recommend .16 or finer layer height and using a glossy filament if available. The reason for these recommendations is that the smoothness of the internal surface of the pipe will affect the speed and consistency at which the brass drops through the pipe. It is also highly recommended to use a 10–15 lines brim on this part for better surface adhesion. The part should be printed with the flat end of the tube on the print bed surface and no support should be used.

Sorter – Homing Bracket
Recommended to use a tough filament such as PLA+ or PETG but really any filament should work as long as you don’t overtighten the m6 mount screw.

Sorter – Sort Bin
These optional sort bins can be used to sort the brass into. They are designed so that they can be oriented at the correct angles to the sorter arm. Recommended to use a layer height between 2 – 3 and print with 0 infill to reduce print time. Typical print time for each bin is roughly 6.5 hours. If you use “vase mode” in Cura, this can be reduced to 2-3 hours per bin, but the bins will be much weaker.

### Sorter Assembly

Here below are the basic steps for building the Sorter Assembly.

1. Ensure you have a working tight fit between the sorter and the mounting arm
2. Install the motor to the sorter
3. Install the Flange into the sorter pipe bracket
4. Install the bracket onto the motor
5. Install the 8 slot sorter base
6. Install the homing sensor and bracket
7. Install the sorter pipe

Ensure Sorter / Pole Mount fitting are snug
Depending on your printer and filament, the fitment between the Sorter Base and Pole Mount may be very tight or slightly loose. If the fit is loose, this is easily remedied with the use of a set screw.

If the fit is so tight that you cannot insert the pole mount into the sorter base, you may need to remove some material from the pole mount. Also check the sorter base to ensure there are no artifacts remaining from the printer support material. When cleaning up the pole mount, start with the leading edges and corners first as this tends to be the areas which grow during printing. Usually after deburring the corners, the fit will be much better. If it is still too tight, use some 150-250 grit sandpaper to clean it up further until the parts fit.

Install the Motor
Use (4) M3x12mm screws to mount the motor. It is recommended to use washers to provide additional holding power when the motor heats up. Make sure you orient the motor in such a way that you will be able to connect the motor cable after the motor is installed. Generally, it is recommended that you orient the motor so the connector is facing out to the side.

Install the Flange
Use (4) m3x12 screws to attach the flange to the bottom of the Sorter Bracket Pipe Bracket. Make sure the flange coupler has the included Allen set screws installed but set so that the flange can be slipped over the motor shaft.

Connecting the Sorter Pipe Bracket to Motor
Typically, the motor shaft will have a flat side. Ensure that one of the Allen set screws are aligned with the flat on the motor shaft. Tighten down the set screws while adjusting the height of the flange so that the set screws are just above the top of the sorter base.

Install the Sorter Base 8 Slot Ramp
Slide the 8 Slot base over the Sorter pipe bracket and align the two m5 screw holes with the holes in the base. Only install the right (with mount side facing you) m5x20 screw. The homing bracket will be secured by the left screw.

Install the Homing Sensor and Bracket
Using (2) M3x7 (M3x10 will work too), mount the homing sensor to the homing bracket so that the mount point is to the left of the sensor when the sensor connector is facing you.

Thread the M5x20 screw through the Homing Bracket. The homing bracket should spin freely around the m5 screw. If not, you can “strip” it by continuing to turn the screw after the homing bracket is fully seated. Thread the screw into the left hole on the sorter base while holding the homing bracket in place. Do not overtighten as you can crush the homing bracket. Tight the screw down until the homing bracket moves under tension. Pivot the homing bracket over the other screw so that the homing bar lightly contacts the Sorter Pipe Bracket. Turn the sorter pipe bracket until the homing bump contacts the homing sensor. Ensure you have proper alignment with the first slot.

Install the Sorter Pipe
Insert the (2) M3x15mm screws in the designated holes on both sides of the Sorter Pipe Bracket. Thread the screws until the end of the screw is flush with the inside of the pipe channel. Position the pipe in the channel so that the top edges of the pipe are aligned and parallel to the sorter pipe bracket. Tighten the down the set screws on both sides of the bracket so that the pipe does not move.

Pole Mount
The sorter is the first item to be installed on the 1” pole. Use M6x25 screws with butterfly nuts to tighten the mount to the pole.

## Electronics and Enclosure Assembly

### Printing the Enclosure Models – General Settings

The electronics enclosures can be printed in any material and color of your choosing. This is entirely personal preference and I make no recommendations here.

Enclosure – Box
This box houses the electronics. If it is printed to spec, it should match up to existing Arduino uno holes. It is
recommended that you should use a support angle of 88 degrees. The only support area needed is the USB hole.

Enclosure – Lid
Recommend printing along with the box with the same material so after accounting for shrinkage, everything works.

### Electronics Assembly

Refer to the Parts List section below for the list parts and resources to acquire the needed components to complete this project

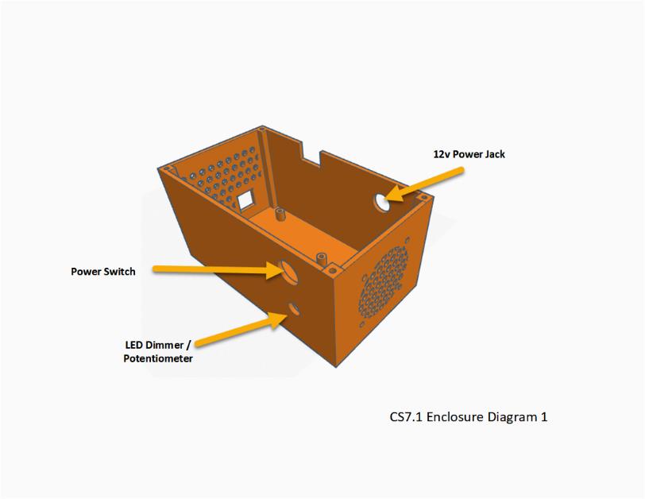
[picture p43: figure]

QUICK STEPS
1. Create your rails
2. Install 40mm Fan
3. Install LED Dimmer with 4.7K resistor.
4. Install 12v Jack
5. Install Power switch
6. Install Arduino Uno
7. Install Motor Shield
8. Install jumpers
9. Install TCM2209 Motor Controllers
10. Connect all 12v power lines and ground
11. Attach Sensor Cables
12. Attach motor cables to shield
13. Adjust Vref on motors
14. Load Arduino code onto Arduino

Detailed Instructions

Create or designate a 12v Rail
The 12v rail can be a wire nut, traditional terminal rail or the lever wire nut connectors which I prefer.

https://amzn.to/40GJgQx

This will be the connector where all your 12v connections will join.

Create a 5v Rail
Connect a yellow wire from the 5v pin on the motor shield to your 5v Rail. The 5v rail can be a wire-nut, traditional terminal rail or the lever wire nut connectors mentioned earlier.

Create a ground rail
Just like our other rails, this rail will be where all our ground connections will be made.

Install 40mm Fan
The 40mm fan should be installed on the inside of the enclosure. The back of the fan has hex shaped holes where the 3mm nuts should be placed the front of the fan should face the enclosure wall grill. You will need (4) M3 screws of approximately 15mm length. The fan’s red wire will be connected to the 12v rail and black to ground. You can wait to connect these if you want and I prefer to do it towards the end for better wire management

Install LED Dimmer
Before installing the PWM dimmer, you will need to connect the low voltage solder jumper point on the bottom of the PWM dimmer. From the manufacturer’s instructions, the solder point is highlighted in the screenshot below and a bit of solder needs to be added between these two points:

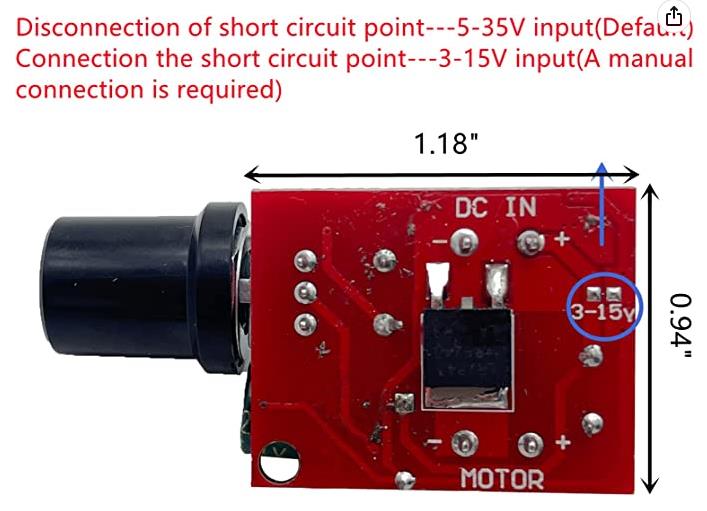
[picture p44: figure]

Connect the yellow and black wires to the power side of the dimmer. The wires should be approx. 4-6 inches in length to and they can be cut down to size later. These wires will connect to your 5v rail and ground. On the motor/led side of the dimmer, connect two smaller wires (22-24AWG) of approximately 6-8in. You will need to install the .25watt 1.2K resistor between the negative output and the connector which will provide a more useable light range. It is recommended to use yellow and black to signify low signal and ground though you can use whatever colors you prefer of course. I generally use a 4 wire motor cable to feed this signal where two of the wires are feeding the camera housing fan (12v+,- ) and the other two are connected to the dimmer output and the light right. For a standard motor cable, I cut the motor connector side off and wire strip those wires to install to my 12v rail and my dimmer.

Install Power Jack (12v)
If you are not using the power jacks with pre-soldered wires, you will need to solder 6” 16AWG wires to the leads. Red wire on the center pin and black on the outer.

Install Power Switch
Solder 16AWG red wires of approx. 6” length to both leads on the power button. Install into the enclosure and secure with a nut.

Install the Arduino Uno
The Arduino Uno should drop right into the box and us the USB hole for alignment. The Arduino is secured by M3 x 5mm screws. Do not over tighten these or you will break the screw risers. If you can get all 4 screws in, don’t fight it. It will be plenty secure with just two screws. Magnetic screwdriver helps here.

Install the CNC Motor Shield
Before seating the motor shield, you should attach the two 16AWG wires (red & black) of approx. 6” length to the power connector on the shield. This can be difficult to do after it has been seated.

Align the pins and carefully press down on to the Arduino. If you have it lined up, it should only take mild pressure to seat it.

Install Jumpers
There are 7 jumpers in total which must be installed. 3 will go under each motor controller (C1 & C2) which are generally labeled X and Y on the motor shield. The 7th jumper will go on the EN/GRN pins adjacent to the reset button on the shield. (see Diagram 1 below)

Install the TMC2209 Motor Controllers
Once you have the jumper installed, you can install the controllers simply by aligning the pins and pressing them in.

Connect power wires and ground
The red wire from the power jack should connect directly to one of the red wires on the power switch (it doesn’t matter which). The other red wire coming off the power switch should connect to your 12v Rail. In this way the 12v power will only be available when the switch is on.

Feed Homing Sensor
The homing sensors for this project come with a 3-color wire which is usually red, white and black. Red is a 5v feed, black is ground and white is signal.

Connect the red wire to your 5v rail, connect the black wire to your Ground rail and connect the white wire to Y+ (D10)

Sorter Homing Sensor
Just like the feed homing sensor above, with the only difference being that your white wire will connect to Z+ (D11)

Feed Sensor (Proximity Sensor)
The proximity sensor needs more voltage to work effectively. They are typically wired as Brown->12v, Blue->Ground, Black->signal.

Connect the brown to your 5v rail, blue to ground and black to X+ (D9)

Attach Motor Cables
Before attaching motor cables, ensure the system is disconnected from USB and 12v power

There are many types of motor cables available but the most common motor cable has the wiring ordered as: BLACK, GREEN,BLUE,RED. This cable should be connected next to the controller so that the red wire side of the cable is closer to the outer edge of the shield. (See diagram below). The feed motor is on the X motor controller while the sorter motor is connected to Y. All motors may not be wired the same and may require that you relocate pins on the connector. If your motors are not running smoothly, see the troubleshooting section at the end of this document.

Optional 5v Power
Though it is not usually necessary, some computers may not provide adequate 5v power to keep the Arduino running reliably. If this is the case, you may elect to add a 5v external power supply. To connect this, you would attach the 5v signal to 5v pin as indicated in the diagram below and ground from the power supply would connect to the ground rail.

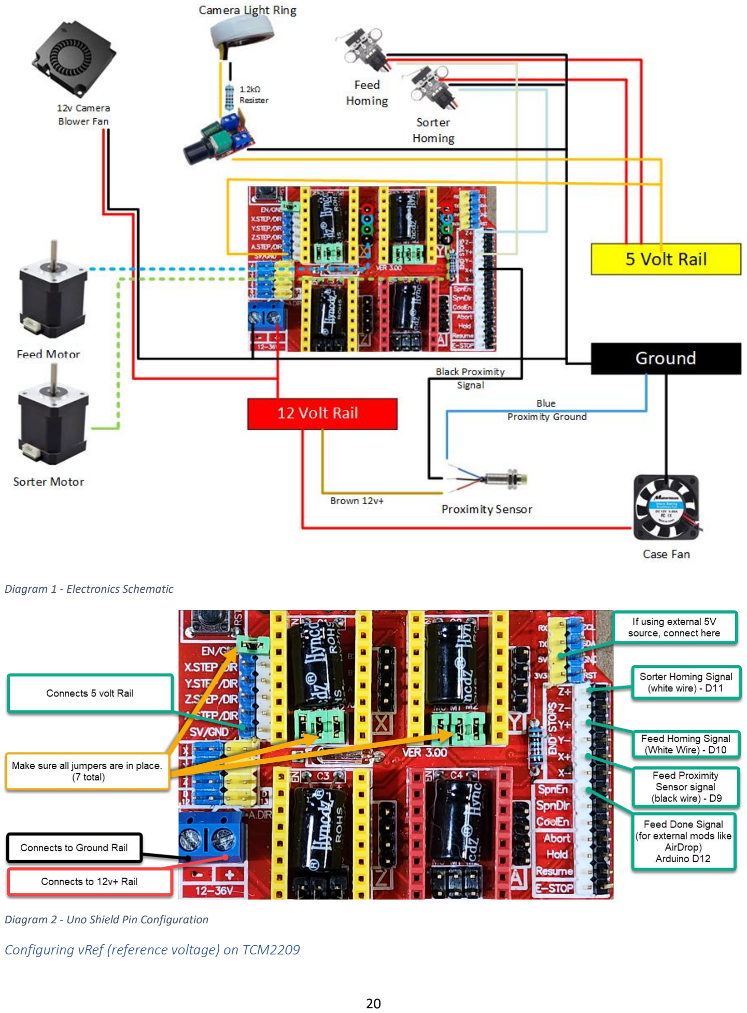
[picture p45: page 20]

Diagram 1 - Electronics Schematic

Diagram 2 - Uno Shield Pin Configuration

Configuring vRef (reference voltage) on TCM2209

Reference voltage determines or measures the amount of current the motor will receive. Usually this is the last thing you will check before closing the lid on the enclosure. Here is the procedure:

1. Power off the system (unplug the 12v and USB cables)
2. Unplug the cables from both motors (sorter and classifier)
3. Power on the system and connect USB.
4. Using a multimeter in DC mode, measure the vRef by placing the negative lead on the 12v negative input
5. Place the positive lead on the vRef measurement port.
6. Reference the Diagram and cheat sheet below to determine the current.
7. Generally, the target vRef should be between .9 and 1.2 amps. It is best to use the lowest amperage the system will operate smoothly under to reduce heat and stress on the motors. To low and the motors will lose steps, too high and the motors will lose steps and overheat.

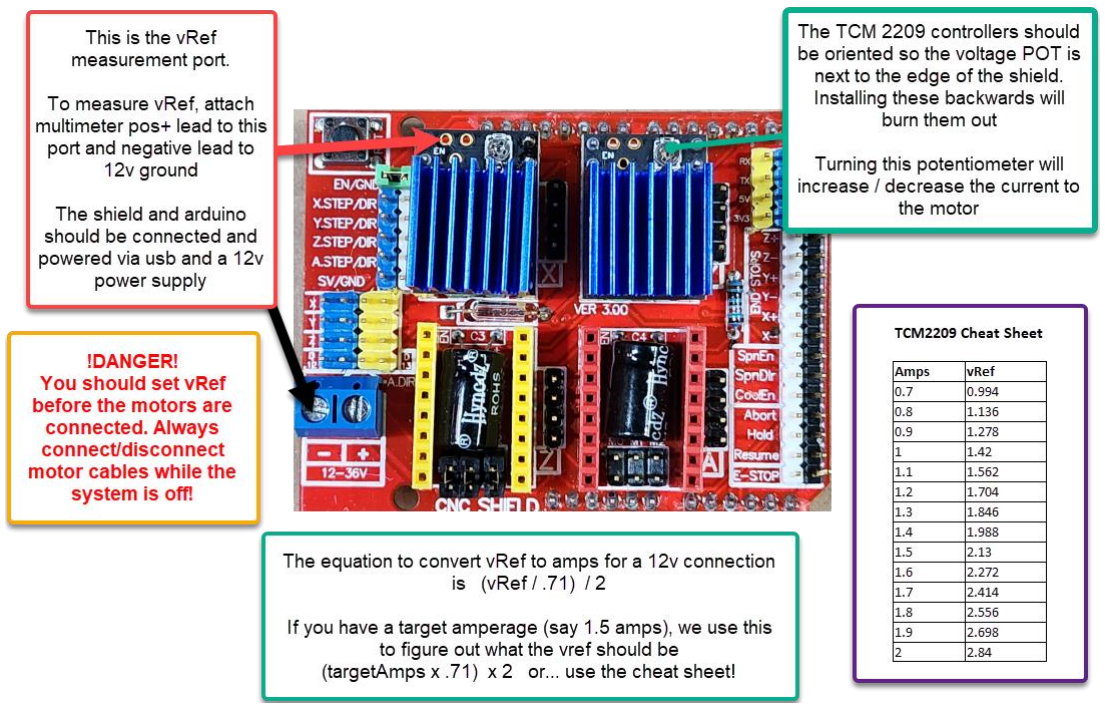
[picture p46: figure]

### Uploading Code to the Arduino

The general steps to program the Arduino are as follows:

1. Download and install the Arduino IDE from https://www.arduino.cc/en/software
2. Download the CS7.1 sorter Arduino code (https://github.com/sjseth/AI-Case-Sorter-CS7.1/blob/main/ArduinoCode/CS71_Arduino/CS71_Arduino.ino) (https://github.com/sjseth/AI-Case-Sorter-CS7.1/blob/main/ArduinoCode/CS71_Arduino/CS71_Arduino.ino)
a. Here is the raw link to get the file: https://raw.githubusercontent.com/sjseth/AI-Case-Sorter-CS7.1/main/ArduinoCode/CS71_Arduino/CS71_Arduino.ino (https://raw.githubusercontent.com/sjseth/AI-Case-Sorter-CS7.1/main/ArduinoCode/CS71_Arduino/CS71_Arduino.ino)
b. The file must be placed in a folder named CS71_Arduino)
3. Double-click to open the CS71_Arduino file in the Arduino IDE
4. Connect your USB cable to the electronics and to your computer
5. Configure the Arduino IDE to talk to your Arduino
6. Upload the code to the Arduino.
7. Test the sorter in the Arduino Serial Console.

Download and Install Arduino IDE
The Arduino IDE (Integrated Development Environment) is the software which is used to create/modify the code which is then programmed to the Arduino board. This is a free software download and is available from the Arduino web site at: https://www.arduino.cc/en/software. The recommendation is to use the latest version which at the time of this writing is 2.0.4.

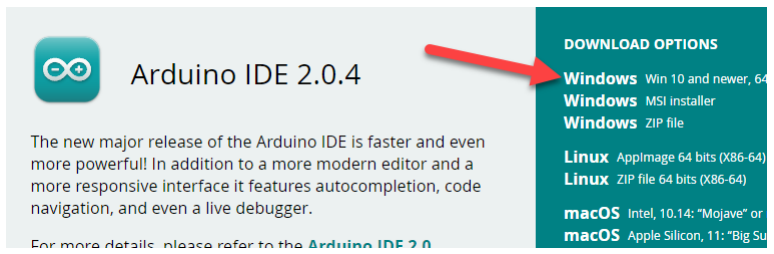
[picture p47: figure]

Download the CS7.1 sorter Arduino Code
If you have downloaded the entire repo as recommended earlier, the Arduino code will be in the folder path where you unzipped the files at: /main/ArduinoCode/CS71_Arduino/CS71_Arduino.ino otherwise you can download the individual file at https://github.com/sjseth/AI-Case-Sorter-CS7.1/blob/main/ArduinoCode/CS71_Arduino/CS71_Arduino.ino (https://github.com/sjseth/AI-Case-Sorter-CS7.1/blob/main/ArduinoCode/CS71_Arduino/CS71_Arduino.ino) . The file will need to placed in a folder named CS71_Arduino. Once you have done that, you can double-click the file to open it.

Connect the Arduino to your computer via USB cable.
In the Arduino IDE, use the device menu to select your Arduino type (UNO)

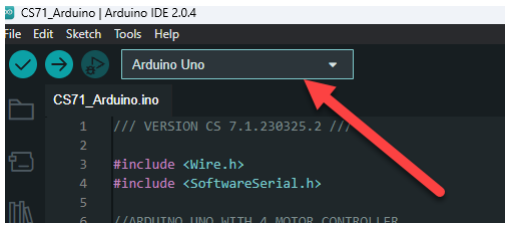
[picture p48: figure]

Upload the code(firmware) to the Arduino microcontroller
Use the upload button in the Arduino IDE to upload the code/firmware to your Arduino device.

How to modify code for testing without sensors connected
If you are interested in loading the code and testing it before you have completely wired up your Arduino, you can simply change the three variables listed below to have a value of “false”. After changing those variables, you can upload the code and test in the Arduino Serial Monitor by sending commands like “0”, “1” or “sortto:4”.

*Note: The Arduino code is often updated and the line numbers may not match the screenshots. The variable names should not change (eg: FEEDSENSOR_ENABLED, FEED_HOMING_ENABLED)

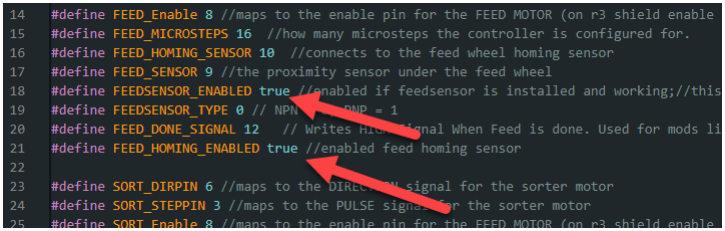
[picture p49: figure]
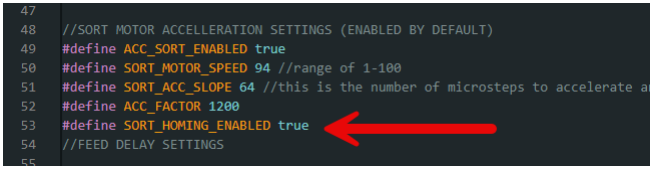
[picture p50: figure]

Testing the Sorter in Serial Monitor Console
You can launch the Serial Monitor with a keyboard short CTRL+SHIFT+M or from the Tools menu.

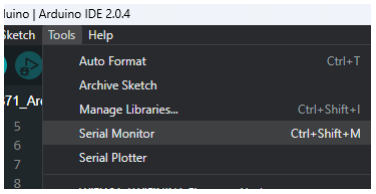
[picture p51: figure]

If the code has been loaded to the Arduino properly, you should see a “Ready” prompt response in the serial console.

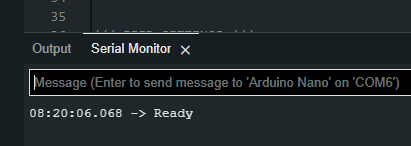
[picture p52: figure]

You can now test the system by sending a number command like “0”. This will cause the system to feed one position. If you send “1” two times in a row, the system should feed two times but on the second time, the sorter arm will also move to the #1 slot position. This is because there is a 2-slot queue so that the sort is delayed by one command.

If you only want to test the sorter arm movement, you can send “sortto:3” command which will move the sorter arm to the #3 slot position. After each command is received and processed, you should receive a “done” response.

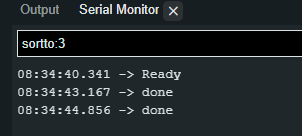
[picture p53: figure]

List of Serial Monitor Commands {number}
(example: 5)

Sending any number causes the system to feed one position and queue a sort to that number on the next feed.

sortto:{number} (example: sortto:5) | Moves the sorter arm to the specified {number} slot position
xf:{number} (example: xf:3) | Force feed to the specified number. (overrides/ignores the feed sensor status)
test:{number} | This command is designed to test the system. Based on the number passed, it will run through that number of feed cycles while moving the sorter arm to a random position between 0-6.
sorttest:{number} | This command will move the sorter {number} of times to a random slot position. Used to test the sorter tracking and if it is losing steps.
homefeeder | Initiates a homing for the feed wheel
homesorter | Initiates a homing for the sorter arm
getconfig | Returns a config which represents the current sorter and feed speed as well as the motor steps for each. Example response: {"FeedMotorSpeed":92,"FeedCycleSteps":60,"SortMotorSpeed":94,"SortSteps":20}

## Parts List

The parts list has been moved to reloadingrecipes.com which will be easier to maintain going forward.

Here is the link:
https://www.reloadingrecipes.com/HeadstampSorter/Partslist

## Troubleshooting

Motors not running smoothly or correctly.
The most common problem when setting up a new system is with the motor cabling. There are many inconsistencies in the cables, connectors and motor internal wiring which cause these issues. The motors have two coils / phases which each have a positive and negative terminal. The issue arises because the 4 pins are not always wired the same.

The most common fix if your motors are jittering/shaking, is to reverse the two inner pins on the motor side of the connector cable. In the Discord forum this is known as the (RGBB) problem, whereby default the cable is configured as RED, BLUE, GREEN, BLACK and needs to be switched to RED, GREEN, BLUE, BLACK as seen on the white connector in the screenshot below.

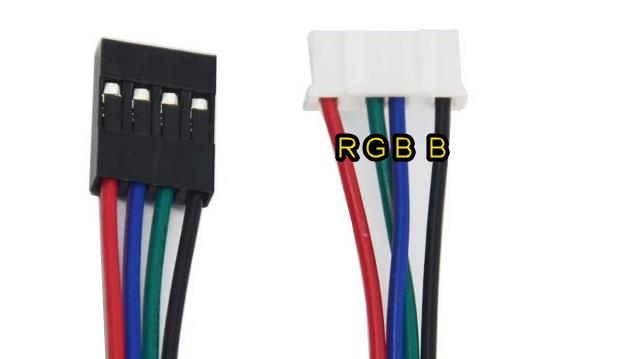
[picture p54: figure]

To swap the wires, you can simply pry up the plastic retention tabs and pull the wires out of the connector. Push the retention tabs back down and insert the wires back into the proper place in the preferred order.

Motors running backwards.
The sorter motor should rotate counterclockwise from slot 0 (homing slot) to slot 1, 2, 3 etc. If when sending a command such as sortto:5, the motor turns clockwise, you will need to reverse the connect on the controller side (in the picture above, it would be black connector). Simply turn off the system, unplug the connector and rotate it 180 degrees and plug it back into the controller. There is no need to swap pins or wires for this condition.

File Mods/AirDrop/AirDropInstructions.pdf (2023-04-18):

# CS7.1 AirDrop Mod

The airdrop mod consists of two 3d printed parts, an air solenoid valve and a switch/relay to active the solenoid. The air pressure on the compressor seems to work best when set between 25 – 40psi.

### AirDrop – Bracket

This can be printed in any semi-flexible filament such as PLA+ or PLA. PETG may be too brittle and cause the clips to break. This module is printed with 20% infill with layer height of .2. It is designed to snap on to the front of the feed bracket.

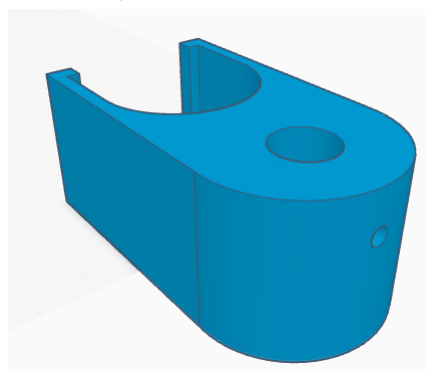
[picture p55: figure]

### AirDrop – Air Nozzle

This part connects to the .25”/6mm air hose using a friction fit. The part can be printed in any material and because it is so narrow and tall, it is recommended to use at least a 10 line brim to help it stick to the print surface. The long end of the tube is inserted into the bracket and secured using an M3 screw.

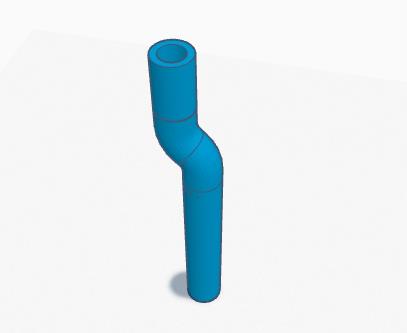
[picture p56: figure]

### Air Solonoid

There are many options for air solonoids but I recommend using a 12v Normally Closed solenoid so you can use the same power source as that currently feeding your electronics system.

https://amzn.to/41BXuTY

You will also need a length of airhose and the connectors to attach the solenoid. I used the following kit but you can probably source the parts you need for your specific compressor setup

6mm pneumatic air hose pipe kit.

https://amzn.to/3MVGpjE

### Mosfet Switch or Relay

This is another choice to make as there are many solutions here. The Arduino has a signal pin on pin 12 which sends a 5v signal at the end of each feed cycle. The solution you use should be controlled a 5v signal and be able to handle a 12v 10w load.

I used a very inexpensive MOSFET Transistor switch and it works very well and was small enough to cram into the electronics housing.

https://amzn.to/3Ac9f7Y

### Wiring Schematic

The below schematic is the wiring diagram for this particular switch but wiring should be similar for any relay. Note, we are running 12v power and Ground from our 12v rail and ground rails.

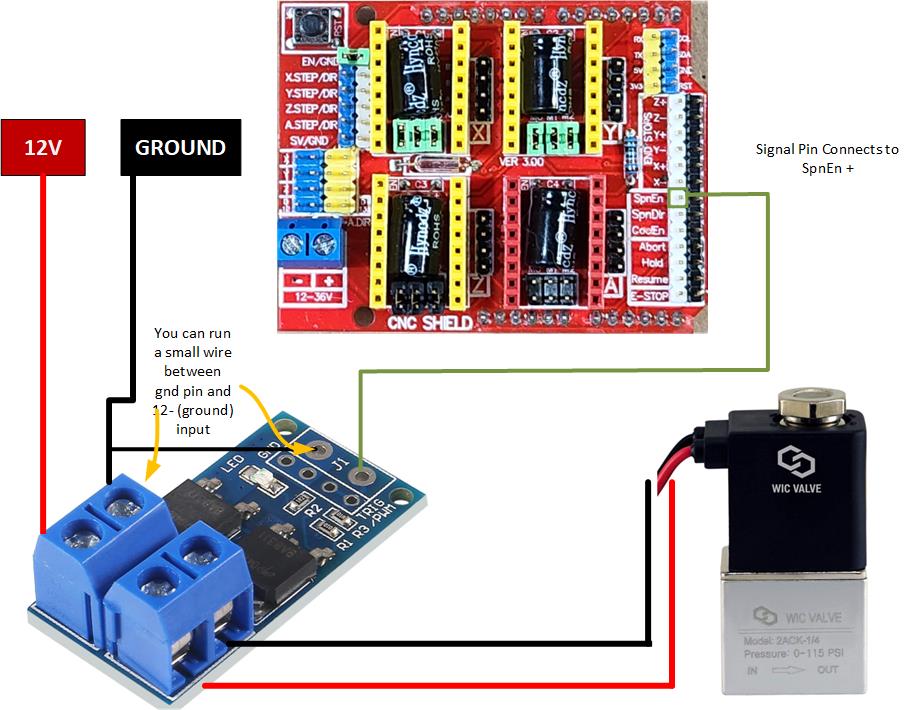
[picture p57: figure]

### Configuring the Arduino

Finally, you will want to adjust the Arduino code to maximize performance in your system.

The following four parameters control the delay settings.

- The length of the air blast is controlled by FEED_CYCLE_COMPLETE_SIGNALTIME (line 55) and is in milliseconds
- The time to wait after feed stops before issuing the blast is FEED_CYCLE_PRESIGNALDELAY. Adding a bit of time here allows for the brass to start dropping before sending the air blast.
- FEED_CYCLE_NOTIFICATION_DELAY is the time to wait after the blast before sending the “done” signal back to the software. This is used to allow time for vibrations to clear before taking the next picture. Setting this too low may result in blurry pictures and too high is just a waste of time.
- SLOT_DROP_DELAY is the minimum amount of time to wait before moving the feed arm in between sorts. Without airdrop enabled this is usually set to about 450-500ms to allow brass to clear the tube before moving the arm.

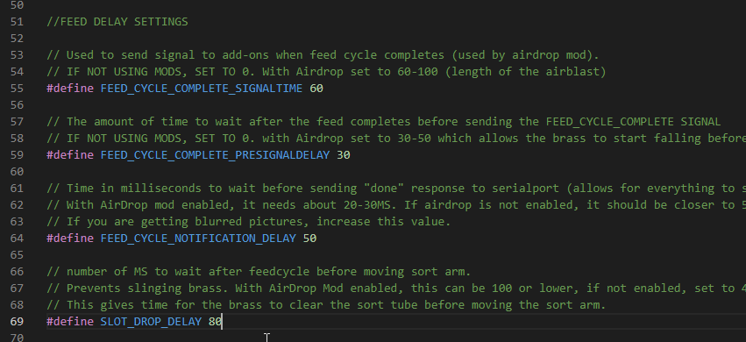
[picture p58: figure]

Once you have set your parameters, you can test in the Arduino console by sending commands like 0 or any number between 0 – 7. Also commands like “test:20” can be helpful as it will run 20 brass through as quickly as possible.

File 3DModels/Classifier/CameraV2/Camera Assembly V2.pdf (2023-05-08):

# Camera Assembly V2

Camera AssemblyV2
The following diagram illustrates the parts required to complete this part of the build. Note that the V2 camera uses a different camera body and light ring than the standard v1 camera.

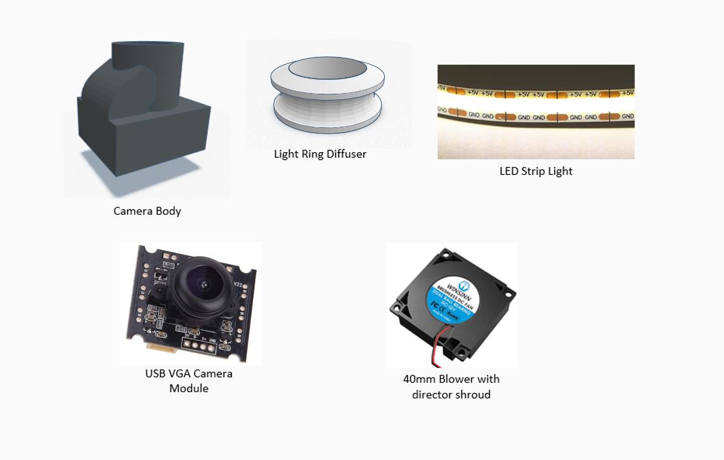
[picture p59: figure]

Here is an overview of the basic assembly steps to complete the v2 camera module

1. Focus the camera
2. Assemble the Light Ring
3. Install the light ring and wiring
4. Install the camera
5. Install the Fan
6. Test

Focusing the Camera
Connect Camera USB cable and connect to a computer and open the default windows camera app. Select the VGA camera.

Set the focus of the camera by using the camera housing as a guide. You can rotate the camera lens to focus the camera. Set the camera body on its side and set or hold a piece of brass approx. 4mm from the top edge of the body. Place the camera into the body and check the focus on your computer.

Once you have the camera reasonably focused, you can unplug it and set it to the side.

Assemble the Light Ring

1. Unroll the USB strip light and cut a section length of 6 sections using scissors or a box cutter.

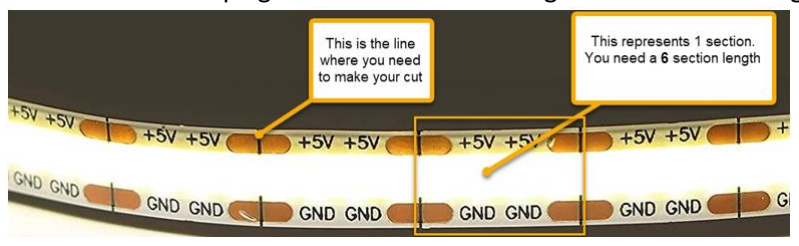
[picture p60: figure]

2. Solder a wire pair to the 5v and ground tabs. The wires should be at least 5 inches long. Recommend using yellow and black wire so the wiring is not confused later with the fan wiring but of course any color will work.
3. Wrap the light strip around the light wring with the strip facing into the ring. Tightly wrap at least 2 circumference lengths of electrical tape around the outside edge of the ring to secure the led strip and wiring in place.
4. Place the light ring into the camera housing with the beveled edge face down and the wires are positioned on the side opposite of the wire exit hole approximately where the green arrow is. Note that the green arrow in the diagram below indicates the surface which the beveled edge of the light ring should be in contact with.

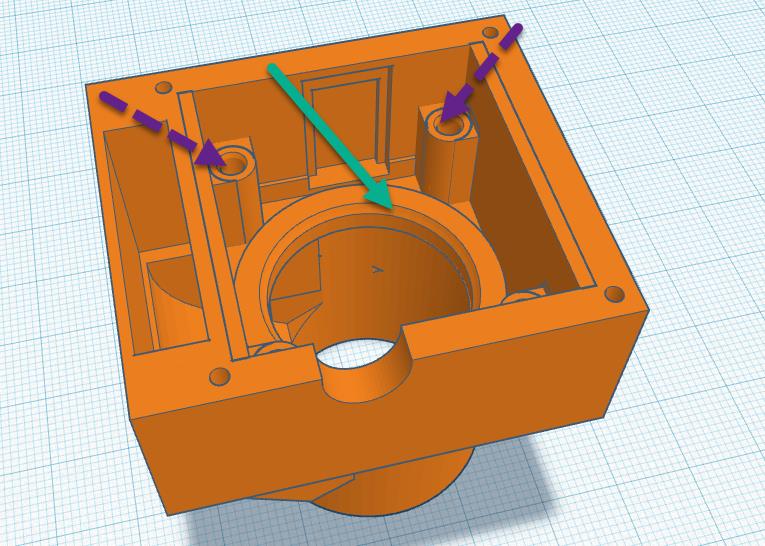
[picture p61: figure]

5. Install two screws in the holes indicated by the purple arrows but do not screw them all the way in, This will serve as a guide for the camera.

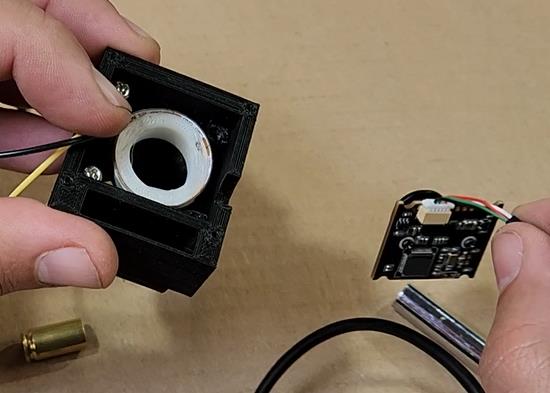
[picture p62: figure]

6. Place the camera into the housing (with the usb cable already connected) making sure the connector side is oriented to the side with the screws.

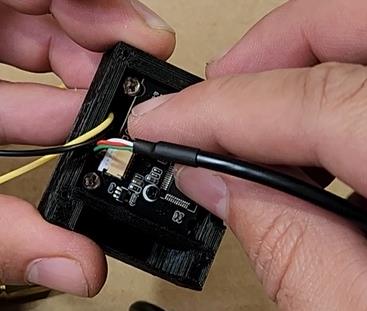
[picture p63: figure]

7. Install the other two screws.
8. Run both the USB wire and the light ring wire out the half-circle hole.
9. Install the fan on top the camera housing using 2mm socket head screws. Make sure the director shroud is oriented correctly.
10. At this point all the wires should close together (fan, light-ring and camera). It may be helpful to put a piece of electrical tape around them to keep them together.
11. Install male Dupont connectors on the fan and light ring wires so they can be easily detached later.

This completes the assembly of the ring. You can test the light ring by applying 5v power to it. The fan requires 12v.

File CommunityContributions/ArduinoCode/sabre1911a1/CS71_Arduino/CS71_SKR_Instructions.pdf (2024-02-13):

P a g e | 1

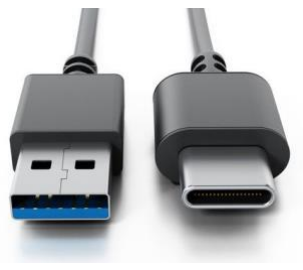
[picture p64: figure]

v1.0.2024.02.06 – Written to work with CS7.1 Parts List and CS7.1 Instructions Manual and Build Guide

# CS7.1 SKR Pico Mod Instructions

## Introduction

This is a guide for building the AI Headstamp Sorter machine created by sjseth but by using a BigtreeTech SKR Pico 3D printer controller board in place of the Arduino Uno and accompanying hardware. The goal for this mod was to use a more purpose-built device with a similar footprint to reduce the parts count and simplify the wiring for the project, add the potential for increased capability via future software updates (2 ARM cores means 2 processes can run independently, UART stepper control, CoolStep, AirDrop without additional hardware, etc.) and possibly realize a small overall materials cost savings in the process.

This guide is meant to be supplementary to the official build guide and is intended only to call out exceptions that are pertinent to this build. Follow the official guide for all steps that are not explicitly outlined in this guide.

This document references the following resources:

- https://github.com/sjseth/AI-Case-Sorter-CS7.1
- https://github.com/bigtreetech/SKR-Pico
- https://learn.adafruit.com/rp2040-arduino-with-the-earlephilhowercore/connecting-your-rp2040 (https://learn.adafruit.com/rp2040-arduino-with-the-earlephilhower-core/connecting-your-rp2040)
- https://docs.vorondesign.com/build/software/skrPico_klipper.html

Computer Requirements
The requirements for this version of the project are the same as for the official project. Please review the official CS7.1 Instructions Manual and Build Guide. (https://github.com/sjseth/AI-Case-Sorter-CS7.1/blob/main/Instructions.pdf)

NOTE: The Arduino Uno in the official project uses a USB A to B cable. For this project, you will need a USB A to C cable instead.

GitHub Repo
It is recommended to download the entire CS7.1 repo so that you have all the files for this project available for printing and reference, as described in the Overview in the official instructions.

## Before You Begin

Prior to ordering parts for this project, review the official Bill of Materials (BOM) found here: https://www.reloadingrecipes.com/HeadstampSorter/Partslist

Cross-reference the official BOM against this exception list and purchase accordingly:

Electronics and Enclosure Parts

Not Needed

- 12mm push button switch
- 12v motor dimmer PWM
- Arduino UNO R3
- CNC Expansion Shield
- TCM 2209 Stepper Motor Drivers
- 2-pin jumpers

Additional/Alternative
Required Parts
- BIGTREETECH SKR Pico V1.0 Controller Board https://www.amazon.com/dp/B09MVJ5XKH
- 16mm 5A push-button switch https://www.amazon.com/dp/B095P1LGR3
- (1) 2-pin JST-XH connector for camera LED
- (1) 3-pin JST-XH connector for proximity sensor
- (4) M3x6 SHCS or longer (case cover)
- (4) M3x15 SHCS (for electronics enclosure fan)

OR

M3x25 SHCS (if you choose a 40X40X20mm fan instead of the 40x40x10mm in the BOM – the electronics enclosure will support either size)

- (4) M3 nuts/lock nuts (case fan)
- (4) M3x12 or longer SHCS (to mount enclosure to pipe bracket)

Classifier and Sorter Parts

Not Needed

- Nema17 motor cables
- LED Strip (5v)

Additional/Alternative
Required Parts
- LED Strip (12v)
This is what I used because it was laying around: https://www.adafruit.com/product/4612

Here's something similar on Amazon (Fair warning: I have not tried this):
https://www.amazon.com/gp/product/B089NNF3FB
- (2) NEMA 17 Motors (1.5a)
Yes, this was not excepted from the official BOM, however the BOM references two products. The one you want for this project is the second one (https://amzn.to/3LxXKxO).

The Two Trees motors come with the correct cables that fit the SKR Pico’s JST connectors without cutting or crimping and will make the build easier.

Optional Parts, Tools and Accessories
Not Needed | • Lever Wire Nut Connectors • DuPont Crimping Tool (tool only) • DuPont Crimping Kits (tool + connectors) • DuPont Connectors • Jumper Wire Kit
Additional/Alternative Optional Items | • JST Crimping Tool with JST-XH Connectors Kit https://www.amazon.com/dp/B0CKYN13N1 • Electrical wire https://www.amazon.com/dp/B0BKGZS7RM

## Building the Classifier

Follow the official instructions.

NOTE: Do not cut existing connectors off of any wires (for example, the camera fan wires) or install DuPont connectors onto any wires (for example, the LED wires). Wiring will be addressed in the Electronic and Enclosure Assembly section of this guide.

NOTE: When building the light ring, remember that you need to use an LED strip rated for 12v for this build. The number of sections needed for the light ring will depend on the type of strip you buy:

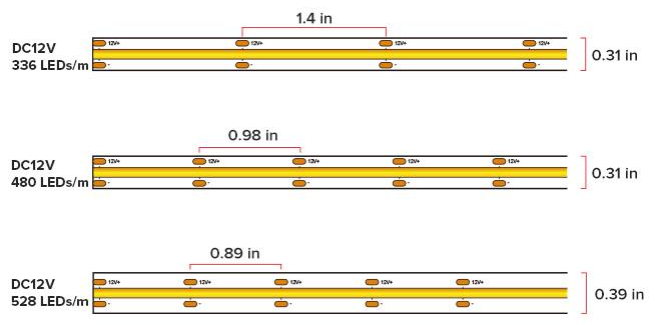
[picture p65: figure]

Image from https://www.amazon.com/BTF-LIGHTING-Flexible-Dimmable-Deformable-Decoration/dp/B089NNF3FB

Wrap the strip around the light ring to see how many will fit around it before you cut.

## Building the Sorter

Follow the official instructions.

## Electronics and Enclosure Assembly

Follow these instructions.

Printing the Enclosure Models – General Settings
The enclosure is three pieces which can be downloaded from the CommunityContributions/Electronics Enclosure/sabre1911a1 section in the AI-Case-Sorter-CS7.1 GitHub (link in Introduction).

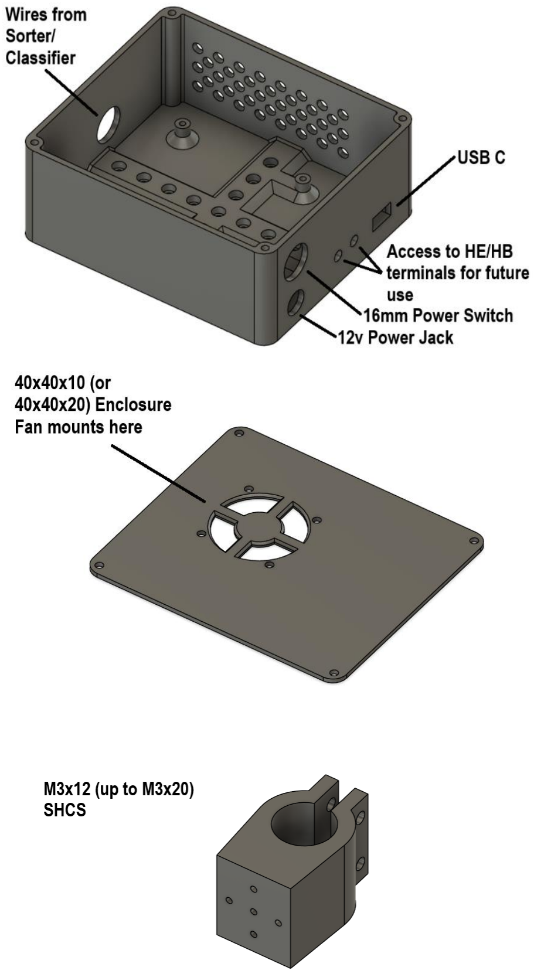
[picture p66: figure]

Body-Electronics_Enclosure_for_SKR_Pico_v1.2.stl

Lid-Electronics_Enclosure_for_SKR_Pico_v1.0.stl

Mount-Electronics_Enclosure_for_SKR_Pico_3.0mm.stl

Or -

Mount-Electronics_Enclosure_for_SKR_Pico_3.2mm.stl

As with the official enclosure, these parts can be printed in any color and material you like. I recommend .2mm layer height, 4 walls, 40% infill, no supports needed if printed in the orientations shown.

Assembly Steps

### 1. Attach the pole mount to the pole using (2) M6x25 SHCS and (2) M6

nuts/locknuts/wingnuts.

### 2. Attach the enclosure body to the pole mount in any appropriate

position/orientation, using (3-4) M3x12 (up to M3x20) SHCS.

### 3. Install 40mm Fan to Enclosure Lid

Attach 40mm fan to the inside of the enclosure lid as shown, using (4) M3x15 SHCS (for 40x40x10mm fan) or (4)M3x25 SHCS (for 40X40X20mm fan) and (4) M3 nuts/lock nuts.

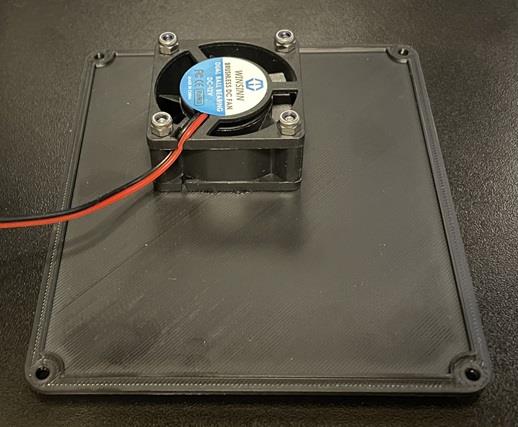
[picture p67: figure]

### 4. Install 12v Jack to Enclosure Body

Place the 12v jack into the bottom hole on the side of the electronics enclosure as indicated in the image on the previous page. Secure the jack with the included lock washer and nut.

### 5. Install Power Switch to Enclosure Body

Place the 16mm latching push button switch into the top hole on the side of the electronics enclosure as indicated in the image on the previous page. Secure the switch with the included lock washer and nut.

### 6. Create Main Electrical Connections

a. Attach the positive (red) lead from the 12v jack to one of the connectors on the switch (depending on what switch you sourced, you may have to solder it or use a screw terminal).
b. Attach (solder or whatever is appropriate) another length of wire approximately 80mm, to the other connector on the switch. Strip the other end of the wire back approximately 5mm.

The circuit should look like this (once the SKR Pico is installed):

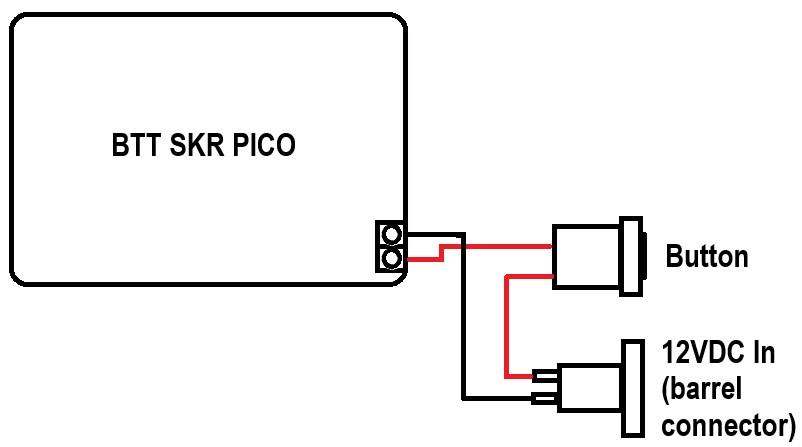
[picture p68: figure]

### 7. Prepare LED Wiring

a. Solder a 1.2K Ohm resistor in-line on the positive lead coming from the camera LED ring. There needs to be wire on both sides of the resistor as shown below, so you can properly crimp on the JST connector in the next step. Install heat shrink tubing over it.
b. Install a 2-pin JST-XH connector onto the fan wires. Mind the wire orientation shown in the image above.

NOTE: If you need a quick tutorial on installing this type of connector (I find it tricky), there are several available on YouTube.

### 8. Prepare Proximity Sensor Wiring

Install a 3-pin JST-XH connector onto the proximity sensor wires. Mind the wire orientation shown in the image below.

### 9. Prepare End-Stop Wiring

Swap the red and white wires in the JST connector on ONE side of each end-stop switch cable (assuming this product from the official BOM: https://www.amazon.com/dp/B07PCN6T6F) as shown in the image below. I chose to do it on the switch end, but it doesn’t matter which you choose.

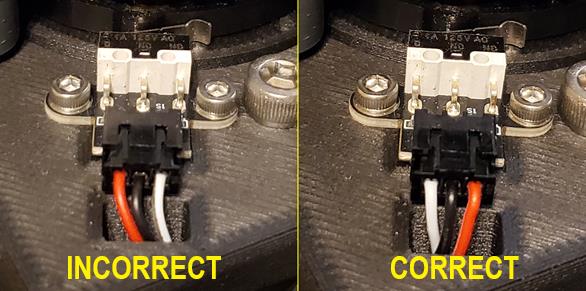
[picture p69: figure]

WARNING: Failure to complete this step will result in very hot wires and possible damage to the SKR Pico.

10.Make Connections

a. Install jumpers (included with the SKR Pico) as shown in the image below.

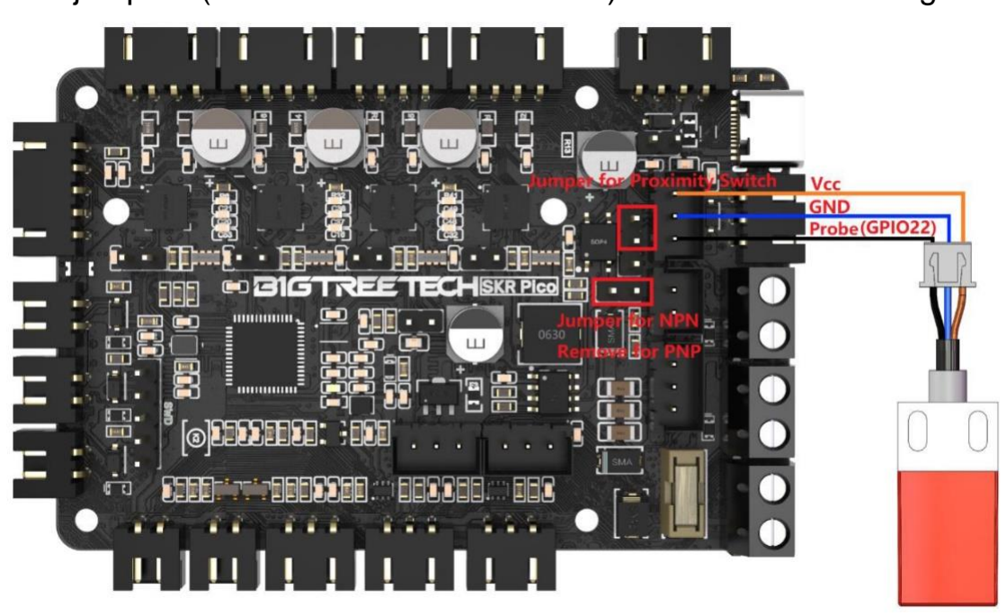
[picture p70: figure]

Image from BTT SKR Pico V1.0 Instruction Manual

b. Pass the stepper motor (4-pin ends), end-stop, camera fan, LED ring, and proximity sensor wires through the access hole in the enclosure.

c. Connect all wires to the SKR Pico as shown in the picture below. Doublecheck each wire color matches the correct pin, as shown (remember which end of the end-stop wires you switched in the previous step when considering this picture).


NOTE: Do not attach the USB cable at this time.

d. Secure the SKR Pico into the enclosure using the included M2.5 screws.
e. If you have not done so already, connect the motors and end-stop switches to their respective cables.

NOTE: Do not put the enclosure cover on yet. Be sure to support the enclosure lid/fan for now (as with brake calipers when changing pads/rotors) – don’t let it dangle by the fan wires.

## Uploading Code to the Arduino SKR Pico

The general steps to program the SKR Pico differ somewhat from the steps to program the Arduino in the official instructions. You will be using both sets of instructions for this process.

Download and Install Arduino IDE
Follow the official instructions.

Download the Arduino Code
If you:
- Downloaded the entire repo as recommended in the Introduction, the correct code for the Pico will be in the folder path where you unzipped the files at: /CommunityContributions/ArduinoCode/sabre1911a1/CS71_Arduino.ino
- Did not downloaded the repo, you can download the
individual file at https://github.com/sjseth/AI Case Sorter CS7.1/blob/main/CommunityContributions/ArduinoCode/sabre1911a1//CS71_ SKR.ino. (https://github.com/sjseth/AI%20Case%20Sorter%20CS7.1/blob/main/CommunityContributions/ArduinoCode/sabre1911a1/CS71_SKR.ino) Place the file in a folder named CS71_Arduino. Once you have done that, you can double click the file to open it in the IDE.

Prepare Arduino IDE for SKR Pico
When you open the IDE for the first time, it may ask you to install updates. Go ahead – this will take a few minutes to complete.

### 1. In the menu bar, click Tools, then Board, then Boards Manager…


### 2. In the Boards Manager search field, type “RP2040” and INSTALL the Arduino

Mbed OS RP2040 Boards package. Wait for the installation to complete.


Flash the SKR Pico
1. Plug the 12v power supply into the 12v jack.
2. Make sure the Pico is off (power switch off).

### 3. Place a jumper (included) on the SKR Pico’s Boot pins (see location on

image below):


Image from https://docs.vorondesign.com/build/software/skrPico_klipper.html

4. Connect the Pico to your computer using a USB A-to-C cable.
5. Turn on the power switch. The LEDs on the end-stop switches should light up, but the motors and fans shouldn’t do anything at this point. You should see a new drive show up in Windows, indicating the Pico has entered its bootloader:

### 6. Go to Tools, Board, Arduino Mbed OS RP2040 Boards, and click Raspberry

Pi Pico.

### 7. Make sure you have the CS71_Arduino.ino sketch open in Arduino IDE, then

flash the SKR Pico using the upload button in the Arduino IDE.


Once the sketch has compiled and flashed, the fans should turn on and the classifier wheel and sorter chute should home.

8. Turn off the power switch.
9. Remove the jumper from the Boot pins.

10.Attach the electronics enclosure cover with (4) M3 SHCS, so that the fan is aligned over the RP2040 chip and stepper driver heatsink.

NOTE: You only need manually to enter the bootloader (shorting the Boot pins) the first time you flash an Arduino sketch onto the Pico. You don’t need to enter the bootloader to load subsequent sketches once it is already running one. As long as the Pico is visible in the IDE (as Raspberry Pi Pico), you just need to follow Step 7 above to flash it again.

Reconnect SKR Pico with Arduino IDE

### 1. Turn the electronics enclosure back on. This time, you will not see a new

drive pop up in Windows Explorer.

### 2. In the Arduino IDE, click Tools, then Port, and select whatever COM port is

associated with the Raspberry Pi Pico, as shown below:


You should see “Raspberry Pi Pico on COM__” at the bottom right of the Arduino IDE window.

How to Modify Code for Testing Without Sensors Connected
Follow the official instructions.

Testing the Sorter in Serial Monitor Console
Follow the official instructions.

List of Serial Monitor Commands
All of the original Serial Monitor commands are referenced in the official manual. This build uses built-in PWM to control the brightness of the camera’s LED ring, as well as the camera and electronics enclosure fan speeds.

The table shows the additional commands added to the software for controlling the LED (you will need this) and fan PWM settings.

Bear in mind that not all fans support PWM control, so the default setting for both fans is full on. It’s probably best to leave the fan settings alone, but the option exists to slow them down if you want to.

camfan:{number} (example: camfan:255) | Changes the speed of the camera fan. Valid input: any integer from 0 to 255 (default 255)
camlight:{number} (example: camlight:100) | Changes the brightness of the camera LED ring. Valid input: any integer from 0 to 255 (default 100)
efan:{number} (example: efan:255) | Changes the speed of the electronics enclosure fan. Valid input: any integer from 0 to 255 (default 255)

Adjusting the Camera Light Ring
This build does not incorporate a physical knob to adjust the LED brightness, but brightness adjustments can be made in the Headstamp Sorter software.

### 1. Connect the camera USB cable to your computer and open the default Windows

camera app. Select the VGA camera.

2. Turn on the electronics box.

### 3. Open the Arduino IDE and launch the Serial Monitor with the keyboard short

CTRL+SHIFT+M or from the Tools menu.

### 4. Insert a piece of brass into the classifier feed wheel over the proximity sensor

and enter a number command – like “0” – into the Serial Monitor, so that the classifier will feed the brass to the next position.

a. Repeat this step once more so that there is a piece of brass held over the camera and the headstamp is visible in the Windows camera app.

### 5. Send camlight:{number} commands to the Serial Monitor, adjusting the integer

up or down until you are happy with the brightness. The default is 100, but the available range is from 0 (off) to 255 (full brightness).


### 6. Once you find a brightness level you are happy with, open the Headstamp Sorter

software and go to Advanced Settings inside Configuration.

### 7. Add a new key/value pair:

a. Key: camlight
b. Value: whatever integer you settled on

### 8. Click Save changes and back on the Configuration page check the Initialize

these Settings on Startup box.

--- END OF LINE ---

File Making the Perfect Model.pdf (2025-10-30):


# Making the Perfect Model

### With AI Headstamp Sorter 1.1.53

# Preparation

When creating a model, it is important to keep “consistency” in mind. This is to say that you want the images you capture to be a near perfect representation of the images that will be captured during the run.
For example, if you are training the model with brass that has been cleaned and shined, you will get best results if you also clean and shine the brass being fed in at run time. As another example, if your light setting is at 50% during training, make sure it is the same at run time. Small changes to the setup between training and runtime can have an impact on accuracy of classification.

# Process Overview

Here is a brief summary of the steps needed to create a flexible and accurate model.
- Create a base model (using proper settings)
- Capture Training Images and define classifications
- Clone and enhance the model.
- Train the cloned model

# Creating a “base”Model

First let’s define a base model. It is a model which you will use as a base to build your run models. The base model will typically be using the standard color mode and leverage primer masking (unless your model is targeted to primers). The base model will typically have 10 – 20+ images per headstamp/classification. Each image will be unique and rotations will not be used here.
Lets go through the steps of setting up the model.
1. On the Models tab, click on the “New” button under the “Create Model” heading.


2. In the create model form, name your model, set processing mode to Color, enable Hide Primer and set mask size to 130. Also ensure Use Deep Learning is selected. (see screenshot)


3. After clicking the Create button, head back over to the Configuration screen and make sure the Enable Image Processing checkbox is checked. Set the Rotations to 1.


4. Next click on the Fine Tuning link to access the capture tuning screen
5. Click the Feed One button until the system has fed a piece of brass over the camera. An image capture should be present in the screen.


You will need to “tune” the settings so that your images are being capture optimally.
- Set the Detection Mode to “Hybrid”
- Click on the center of the primer or primer pocket on the image on the left. This will set the center of your detection area
- Increase or reduce Radius setting until the detection area is just slightly larger than the captured headstamp. The reason it needs to be larger is that not every piece of brass will feed to the same position so you need a buffer around it to ensure that every image will be captured correctly.
- Set Crop Padding to 1. An optimal capture will look like the image on the right in the screenshot above where the arrows show little to no “padding” and the headstamp extends to the edges of the image.
- Set Scan Precision and Scan Sensitivity to 1. This should give you the best capture. You can then increase these values until your captures begin to degrade (off centered). Once you get to that point, you can reduce the value a bit and then use the Feed button to feed 15-20 pieces through the machine to make sure all images are being captured correctly.
- Note that there is a direct relationship to Scan Precision and the Processing Time. As you increase the value of Scan Precision (making it less precise) you will notice the processing time goes down. Ideally you want the highest value here which gives consistently correct images.
- Be sure to hit the Save Changes button before continuing.

6. Now you are ready to begin capturing images for your base model. Click on the Train button to go to the training screen.

# Training Image Capture

While training, you will capture approximately 10-20 examples of each headstamp. You will see a count present in the matrix on the right side of the screen. Once a headstamp gets to 20, you can the Feed button to skip adding additional images for that headstamp and focus on adding more training data for the other headstamps. Continue this process until you have a balanced set of data or run out of brass to capture.

# Classification/Headstamp Creation

You will typically have more success if you avoid “bucket” classifications. For example rather than create a classification for “Federal”, you might consider creating specific classifications such as “FC01”, “FC07”, “Federal-14”, “Federal +P” where the classification corresponds to what is seen on the headstamp. If you wish to sort these all to the same bucket, you can still do that later by selecting all the Federal headstamp variations for a particular slot.

# Clone and Enhance

Once your base model has a sufficient amount of data, we will head back to the Models screen and launch the model enhancer.
Here we are going to clone the base model to a new model and generate rotations as well as balance the model and apply additional image processing (GSBLUR)


If your original base model was set up correctly as indicated earlier in this guide, you will not need to select the Center Images or Add Primer Masks options as those are already included in the base model. The above screenshot has the current recommendations for the best recognition.
- Add Rotations with rotation count set to 8 (in testing little benefit was seen beyond 10 rotations)
- Balance Model
- Processing Mode set to GSBlur with Blur Size: 30 and Blur set to 3

Click the Run button to begin the new model creation using your base model as the source.
The Model Enhancer will begin by cloning the model and then start the enhancement operations.


Once this completed, you will have a model which is nearly ready to Run but still requires that you “Train” the model.
First go back to the model screen and make sure you make the newly cloned model active by selecting it.


Now go to the Training screen and click the “Train Model” button.


Once this operation completes, your model will be ready to use in the Run screen

# Running the Model

The Application Guide covers the various options in the Run screen but since the goal here is to get maximum accuracy, I am going to add a few recommendations about your run settings here as well.
The most accuracy will typically be achieved with the following settings:


Increasing Sample Rotations will give even better results. However, the more rotations that are added, the slower the classifications will be.
Regarding the “Mode” setting, both Serial and Parallel will give the same accuracy however Serial will generally work better on less performant machines while Parallel will be much faster when running on good hardware.

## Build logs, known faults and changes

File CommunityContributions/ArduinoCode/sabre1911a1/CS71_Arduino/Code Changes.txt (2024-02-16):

Code changes from official CS71_Arduino.ino
For SKR Pico Build
02-15-2024

From top to bottom...
-------------------------------------------

REMOVE the #include <SoftwareSerial.h> line

ADD to the top of the code where all the other "#define" statements are:

  //CAMERA FAN
  #define CAM_FAN_PIN 17 //SKR FAN1 HEADER
  #define CAM_FAN_DEFAULT_PWM 255 //Fan speed integer between 0 (off) and 255 (full on) - NOT ALL FANS SUPPORT PWM
  
  //CAMERA LIGHT
  #define CAM_LED_PIN 18 //SKR FAN2 HEADER
  #define CAM_LED_DEFAULT_PWM 100 //Brightness integer between 0 (off) and 255 (full on)
  
  //ELECTRONICS ENCLOSURE FAN
  #define E_FAN_PIN 20 //SKR FAN3 HEADER
  #define E_FAN_DEFAULT_PWM 255 //Fan speed integer between 0 (off) and 255 (full on) - NOT ALL FANS SUPPORT PWM
  
MODIFY the following lines:
  FROM						TO
  ----						--	
  #define FEED_DIRPIN 5				#define FEED_DIRPIN 13
  #define FEED_STEPPIN 				#define FEED_STEPPIN 14
  #define FEED_Enable 8				#define FEED_Enable 15 
  #define FEED_HOMING_SENSOR 10			#define FEED_HOMING_SENSOR 4
  #define FEED_SENSOR				#define FEED_SENSOR 22
  #define FEED_DONE_SIGNAL 12			#define FEED_DONE_SIGNAL 0

  #define SORT_DIRPIN 6				#define SORT_DIRPIN 10
  #define SORT_STEPPIN 3			#define SORT_STEPPIN 11
  #define SORT_Enable 8				#define SORT_Enable 12
  #define SORT_HOMING_SENSOR 11			#define SORT_HOMING_SENSOR 3
  #define SORT_MICROSTEPS 16			#define SORT_MICROSTEPS 8

In the VOID SETUP() {} section:

  REMOVE the "Serial.print("Ready\n");" line

  MODIFY the following lines:
    FROM					TO
    ----					--
    pinMode(FEED_HOMING_SENSOR, INPUT);		pinMode(FEED_HOMING_SENSOR, INPUT_PULLUP);
    pinMode(SORT_HOMING_SENSOR, INPUT);		pinMode(SORT_HOMING_SENSOR, INPUT_PULLUP);
    digitalWrite(FEED_Enable, HIGH);		digitalWrite(FEED_Enable, LOW);
    digitalWrite(SORT_Enable, HIGH);		digitalWrite(SORT_Enable, LOW);
    digitalWrite(FEED_DIRPIN, LOW);		digitalWrite(FEED_DIRPIN, HIGH);

  ADD the following lines:
    pinMode(CAM_FAN_PIN, OUTPUT);
    pinMode(CAM_LED_PIN, OUTPUT);
    pinMode(E_FAN_PIN, OUTPUT);

    analogWrite(CAM_FAN_PIN, CAM_FAN_DEFAULT_PWM);
    analogWrite(CAM_LED_PIN, CAM_LED_DEFAULT_PWM);
    analogWrite(E_FAN_PIN, E_FAN_DEFAULT_PWM);

	while (!Serial) {
	  //Wait until Serial is ready
	}
    
	Serial.print("Ready\n");

REMOVE this whole section:

  int FreeMem(){
    extern int __heap_start, *__brkval;
    int v;
    return(int) &v - (__brkval ==0 ? (int) &__heap_start : (int) __brkval);
  }
  
In the void checkSerial(){} function:

  In the if (input.startsWith("ping")) {} statement:
    REMOVE the following line:
	  Serial.print(FreeMem());

  Immediately after the if (input.startsWith("ping")) {} statement, ADD the following statements:
    if (input.startsWith("camfan:")) {
      input.replace("camfan:", "");
      pwmCamFan(input.toInt());
      resetCommand();
      return;
    }

    if (input.startsWith("camlight:")) {
      input.replace("camlight:", "");
      pwmCamLight(input.toInt());
      resetCommand();
      return;
    }

    if (input.startsWith("efan:")) {
      input.replace("efan:", "");
      pwmEFan(input.toInt());
      resetCommand();
      return;
    }
	
Somewhere after the void checkSerial(){} function, ADD the following functions:

  void pwmCamFan(int pwmValue){
      if ((pwmValue >= 0) && (pwmValue <= 255)){
        analogWrite(CAM_FAN_PIN, pwmValue);
        Serial.println("ok");
      }
      else{
        Serial.println("invalid PWM input");
      }
  }

  void pwmCamLight(int pwmValue){
      if ((pwmValue >= 0) && (pwmValue <= 255)){
        analogWrite(CAM_LED_PIN, pwmValue);
        Serial.println("ok");
      }
      else{
        Serial.println("invalid PWM input");
      }
  }

  void pwmEFan(int pwmValue){
      if ((pwmValue >= 0) && (pwmValue <= 255)){
        analogWrite(E_FAN_PIN, pwmValue);
        Serial.println("ok");
      }
      else{
        Serial.println("invalid PWM input");
      }
  }

In the void stepSortMotor(bool forward){} function, MODIFY the following statements:
  FROM						TO
  ----						--
  if(forward==true){				if(forward==true){
    digitalWrite(SORT_DIRPIN, HIGH);		  digitalWrite(SORT_DIRPIN, LOW);
  }						}
  
  else{						else{
	digitalWrite(SORT_DIRPIN, LOW);		  digitalWrite(SORT_DIRPIN, HIGH);
  }						}

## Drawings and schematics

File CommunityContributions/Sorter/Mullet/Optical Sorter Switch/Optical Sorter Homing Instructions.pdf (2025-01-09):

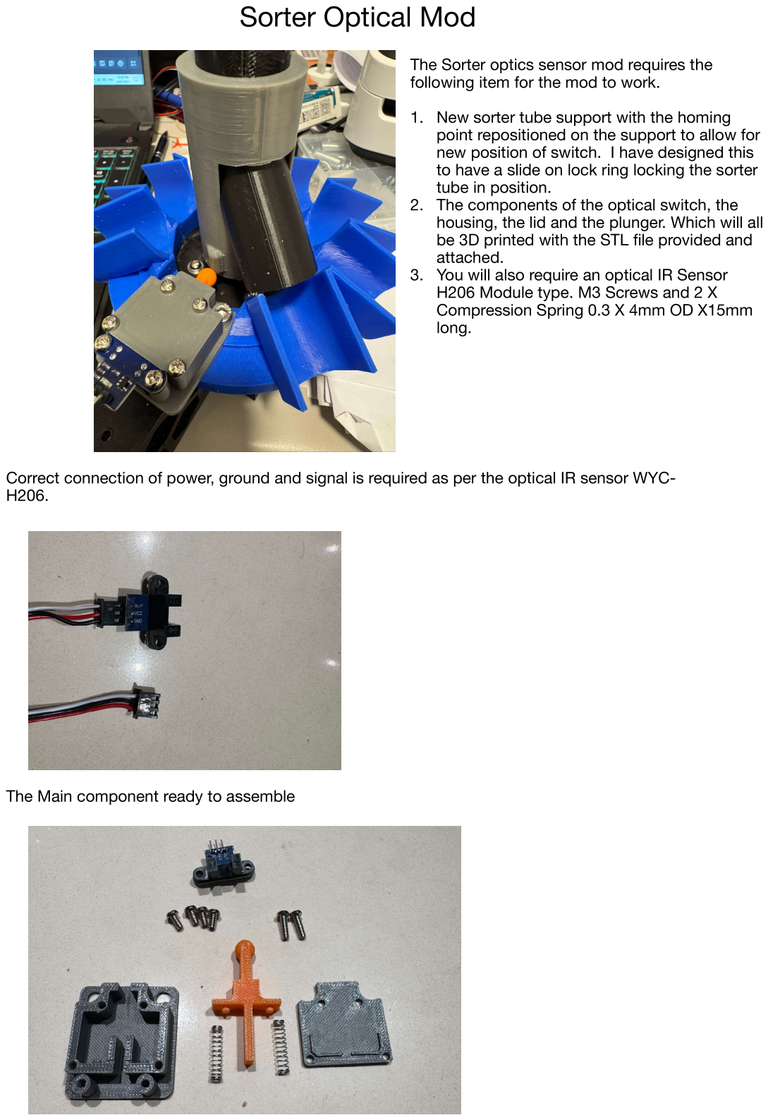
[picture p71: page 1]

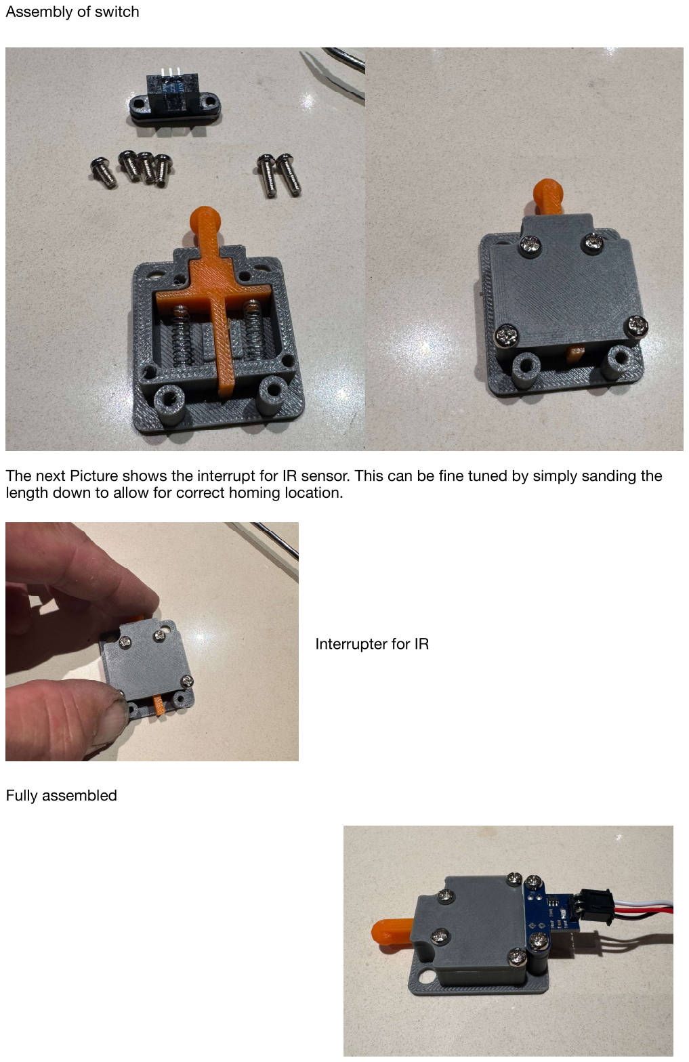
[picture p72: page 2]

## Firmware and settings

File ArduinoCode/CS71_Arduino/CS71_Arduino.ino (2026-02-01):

/// VERSION CS 7.1.260131.1 ///
/// REQUIRES AI SORTER SOFTWARE VERSION 1.1.46 or newer

#include <Wire.h>
#include <SoftwareSerial.h>

#define FIRMWARE_VERSION "7.1.260131.1"

//PIN CONFIGURATIONS
//ARDUINO UNO WITH 4 MOTOR CONTROLLER
//Stepper controller is set to 16 Microsteps (3 jumpers in place)

#define UseArduinoPWMDimmer false //if you have configured your hardware for to use arduino PWM dimmer for light control, set this to true. See: https://github.com/sjseth/AI-Case-Sorter-CS7.1/tree/main/CommunityContributions/ArduinoCode/ausrobbo/LED%20Control

#if UseArduinoPWMDimmer == false 
  #define FEED_SENSOR 9 //the proximity sensor under the feed wheel 
  #define CAMERA_LED_PWM 13 //NOT USED
#else
  #define FEED_SENSOR 13 //the proximity sensor under the feed wheel 
  #define CAMERA_LED_PWM 9 //the output pin for the digital PWM 
#endif

#define CAMERA_LED_LEVEL  78 //camera brightness if using digital PWM, otherwise ignored 


#define FEED_DIRPIN 5 //maps to the DIRECTION signal for the feed motor
#define FEED_STEPPIN 2 //maps to the PULSE signal for the feed motor

#define FEED_MICROSTEPS 16  //how many microsteps the controller is configured for. 
#define FEED_HOMING_SENSOR 10  //connects to the feed wheel homing sensor
#define FEED_HOMING_SENSOR_TYPE 1 //1=NO (normally open) default switch, 0=NC (normally closed) (optical switches) 
#define FEEDSENSOR_ENABLED true //enabled if feedsensor is installed and working;//this is a proximity sensor under the feed tube which tells us a case has dropped completely
#define FEEDSENSOR_TYPE 0 // NPN = 0, PNP = 1
#define FEED_DONE_SIGNAL 12   // Writes HIGH Signal When Feed is done. Used for mods like AirDrop
#define FEED_HOMING_ENABLED true //enabled feed homing sensor

#define SORT_DIRPIN 6 //maps to the DIRECTION signal for the sorter motor
#define SORT_STEPPIN 3 //maps to the PULSE signal for the sorter motor

#define SORT_MICROSTEPS 16 //how many microsteps the controller is configured for. 
#define SORT_HOMING_SENSOR 11  //connects to the sorter homing sensor
#define SORT_HOMING_SENSOR_TYPE 1 //1=NO (default) normally open, 0=NC (normally closed) (optical switches) 
#define SORT_HOMING_OFFSET_STEPS 0 //additional steps to continue after homing sensor triggered

#define AIR_DROP_ENABLED false //enables airdrop

#define MOTOR_Enable 8 //maps to the enable pin for the FEED MOTOR (on r3 shield enable is shared by motors)
#define AUTO_MOTORSTANDBY_TIMEOUT 60 // 0 = disabled; The time in seconds to wait after no motor movement before putting motors in standby
//ARDUINO CONFIGURATIONS

//number of steps between chutes. With the 8 and 10 slot attachments, 20 is the default. 
//If you have customized sorter output drops, you will need to change this setting to meet your needs. 
//Note there are 200 steps in 1 revolution of the sorter motor. 
#define SORTER_CHUTE_SEPERATION 20 


#define FEED_HOMING_OFFSET_STEPS 3 //additional steps to continue after homing sensor triggered
#define FEED_STEPS 70  //The amount to travel before starting the homing cycle. Should be less than (80 - FEED_HOMING_OFFSET_STEPS)
#define FEED_OVERSTEP_THRESHOLD 90 //if we have gone this many steps without hitting a homing node, something is wrong. Throw an overstep error

//FEED MOTOR ACCELLERATION SETTINGS (DISABLED BY DEFAULT)
#define FEED_ACC_SLOPE 32  //2 steps * 16 MicroStes

#define FEED_MOTOR_SPEED 90 //range of 1-100
#define ACC_FEED_ENABLED false //enabled or disables feed motor accelleration. 

//SORT MOTOR ACCELLERATION SETTINGS (ENABLED BY DEFAULT)
#define ACC_SORT_ENABLED true
#define SORT_MOTOR_SPEED 90 //range of 1-100
#define SORT_ACC_SLOPE 64 //64 is default - slope this is the number of microsteps to accelerate and deaccellerate in a sort. 
#define ACC_FACTOR 1200 //1200 is default factor
#define SORT_HOMING_ENABLED true
//FEED DELAY SETTINGS

// Used to send signal to add-ons when feed cycle completes (used by airdrop mod). 
// IF NOT USING MODS, SET TO 0. With Airdrop set to 60-100 (length of the airblast)
#define FEED_CYCLE_COMPLETE_SIGNALTIME 50 

// The amount of time to wait after the feed completes before sending the FEED_CYCLE_COMPLETE SIGNAL
// IF NOT USING MODS, SET TO 0. with Airdrop set to 30-50 which allows the brass to start falling before sending the blast of air. 
#define FEED_CYCLE_COMPLETE_PRESIGNALDELAY 30

// Time in milliseconds to wait before sending "done" response to serialport (allows for everything to stop moving before taking the picture): runs after the feed_cycle_complete signal
// With AirDrop mod enabled, it needs about 20-30MS. If airdrop is not enabled, it should be closer to 50-70. 
// If you are getting blurred pictures, increase this value. 
#define FEED_CYCLE_NOTIFICATION_DELAY 90 

//when airdrop is enabled, this value is used instead of SLOT_DROP_DELAY but does the same thing
//Usually can be 100 or lower, increase value if brass not clearing the tube before it moves to next slot. 
#define FEED_CYCLE_COMPLETE_POSTDELAY 0

// number of MS to wait after feedcycle before moving sort arm.
// Prevents slinging brass. 
// This gives time for the brass to clear the sort tube before moving the sort arm. 
#define SLOT_DROP_DELAY 400

//DEBOUNCE is a feature to counteract case bounce which can occur if the machine runs out of brass and a peice of brass drops a distance from
//from the collator to the feeder. It developes speed and bounces of the prox sensor triggering the sensor and bouncing back up to cause a jam. 
//this seeks to eliminate that by adding a small pause to let the case bounce and settle. 

#define DEBOUNCE_TIMEOUT 300 //default 500. The number of milliseconds without sensor activation (meaning no brass in the feed) required to trigger a debounce pause.

#define DEBOUNCE_PAUSE_TIME 500 //default 500.  Set to 0 to disable. The number of milliseconds to pause to wait for case to settle. 


///END OF USER CONFIGURATIONS ///
///DO NOT EDIT BELOW THIS LINE ///
int cameraLEDLevel = CAMERA_LED_LEVEL; 

int notificationDelay = FEED_CYCLE_NOTIFICATION_DELAY;
bool airDropEnabled = AIR_DROP_ENABLED;
int feedCycleSignalTime = FEED_CYCLE_COMPLETE_SIGNALTIME;
int feedCyclePreDelay = FEED_CYCLE_COMPLETE_PRESIGNALDELAY;
int feedCyclePostDelay = FEED_CYCLE_COMPLETE_POSTDELAY;
int slotDropDelay = SLOT_DROP_DELAY;
int dropDelay =  airDropEnabled ? feedCyclePostDelay : slotDropDelay;

long autoMotorStandbyTimeout = AUTO_MOTORSTANDBY_TIMEOUT;

int feedSpeed = FEED_MOTOR_SPEED; //represents a number between 1-100
int feedSteps = FEED_STEPS;
int feedMotorSpeed = 500;//this is default and calculated at runtime. do not change this value

int sortSpeed = SORT_MOTOR_SPEED; //represents a number between 1-100
int sortSteps = SORTER_CHUTE_SEPERATION;
int sortMotorSpeed = 500;//this is default and calculated at runtime. do not change this value
int homingSteps = 0;

int feedMicroSteps = feedSteps * FEED_MICROSTEPS;

const int feedramp = (ACC_FACTOR + (FEED_MOTOR_SPEED /2)) / FEED_ACC_SLOPE;
const int sortramp = (ACC_FACTOR + (SORT_MOTOR_SPEED /2)) / SORT_ACC_SLOPE;
int feedOverTravelSteps = feedMicroSteps - (FEED_OVERSTEP_THRESHOLD * FEED_MICROSTEPS);
int feedOffsetSteps = FEED_HOMING_OFFSET_STEPS;
int feedHomingOffset = feedOffsetSteps * FEED_MICROSTEPS;

bool FeedScheduled = false;
bool IsFeeding = false;
bool IsFeedHoming = false;
bool IsFeedHomingOffset = false;
bool FeedCycleInProgress = false;
bool FeedCycleComplete = false;
bool IsFeedError = false;
int FeedSteps = feedMicroSteps;
int FeedHomingOffsetSteps = feedHomingOffset;
int feedDelayMS = 150;
int sortDelayMS = 400;

bool forceFeed=false;
String input = "";
int qPos1 = 0;
int qPos2 = 0;
int sortStepsToNextPosition = 0;
int sortStepsToNextPositionTracker=0;
bool SortInProgress = false;
bool SortComplete = false;
bool IsSorting = false;
int sortOffsetSteps = SORT_HOMING_OFFSET_STEPS;
int sortHomingOffset = sortOffsetSteps * SORT_MICROSTEPS;
bool IsSortHoming = false;
bool IsSortHomingOffset = false;
int SortHomingOffsetSteps = sortHomingOffset;
int slotDelayCalc = 0;
bool sorterIsHomed = false;

bool IsTestCycle=false;
bool IsSortTestCycle=false;
int testCycleInterval=0;
int testsCompleted=0;
int sortToSlot=0;
unsigned long theTime;
unsigned long timeSinceLastSortMove;
unsigned long timeSinceLastMotorMove;
unsigned long msgResetTimer;

//debounce variables
unsigned long lastTrigger = millis();
int triggerTimeout = DEBOUNCE_TIMEOUT;
int debounceTime= DEBOUNCE_PAUSE_TIME;
bool proxActivated = false;
bool sensorDelay = false;


void setup() {
  Serial.begin(9600);
  Serial.print(F("Ready\n"));
  
  setSorterMotorSpeed(SORT_MOTOR_SPEED);
  setFeedMotorSpeed(FEED_MOTOR_SPEED);


  pinMode(MOTOR_Enable, OUTPUT);
  pinMode(FEED_DIRPIN, OUTPUT);
  pinMode(FEED_STEPPIN, OUTPUT);
  pinMode(SORT_DIRPIN, OUTPUT);
  pinMode(SORT_STEPPIN, OUTPUT);

  pinMode(FEED_DONE_SIGNAL, OUTPUT);
  pinMode(FEED_HOMING_SENSOR, INPUT);
  pinMode(SORT_HOMING_SENSOR, INPUT);
  pinMode(FEED_SENSOR, INPUT_PULLUP);

  #if UseArduinoPWMDimmer == true 
    pinMode(CAMERA_LED_PWM, OUTPUT);
    adjustCameraLED(cameraLEDLevel);
  #endif

  digitalWrite(MOTOR_Enable, LOW);
  digitalWrite(FEED_DIRPIN, LOW);
  jogSorter();
  IsFeedHoming=true;
  IsSortHoming=true;
  msgResetTimer = millis();
}


void loop() {
   checkSerial();
   getProxState();
   runSortMotor();
   onSortComplete();
   scheduleRun();
   checkFeedErrors();
   runFeedMotor();
   homeFeedMotor();
   homeSortMotor();
   serialMessenger();
   onFeedComplete();
   runAux();
   MotorStandByCheck();
}

int FreeMem(){
  extern int __heap_start, *__brkval;
  int v;
  return(int) &v - (__brkval ==0 ? (int) &__heap_start : (int) __brkval);
}

bool commandReady = false;
char endMarker = '\n';
char rc;

void recvWithEndMarker() {
    while (Serial.available() > 0 ) {
        rc = Serial.read();
        delay(1);
        if (rc != endMarker) {
            input += rc;
        }
        else {
            commandReady=true; 
            return;
        }
    }
 }
void resetCommand(){
  input="";
  commandReady=false;
}

void checkSerial(){
  if(FeedCycleInProgress==false && SortInProgress==false && Serial.available()>0){
   
      //input = Serial.readStringUntil('\n');
       recvWithEndMarker();
       
       if(!commandReady){
        return;
       }
      // Serial.print(input);
       
     //this should be most cases
      if (isDigit(input[0])) {
        moveSorterToNextPosition(input.toInt());
        FeedScheduled = true;
        IsFeeding = false;
        scheduleRun();
        resetCommand();
        return;
      }

      if (input.startsWith("version")) {
       
        Serial.print(FIRMWARE_VERSION);
        Serial.print(F("\n"));
        resetCommand();
        return;
      }

      if (input.startsWith("homefeeder")) {
        feedDelayMS=400;
          IsFeedHoming=true;
         Serial.print(F("ok\n"));
         resetCommand();
         return;
      } 
      if (input.startsWith("homesorter")) {
        sortDelayMS=400;
        jogSorter();
        qPos1 = 0;
        qPos2 = 0;
          IsSortHoming=true;
          Serial.print(F("ok\n"));
          resetCommand();
         return;
      } 
      if (input.startsWith("stop")) {
      resetCommand();
          FeedScheduled=false;
          IsFeedHoming=false;
          IsFeedHomingOffset = false;
          IsSortHomingOffset = false;
          FeedCycleComplete=true;
          FeedCycleInProgress = false;
         // Serial.print("ok\n");
         return;
      } 

      if (input.startsWith("sortto:")) {
          input.replace("sortto:", "");
          moveSorterToPosition(input.toInt());
           Serial.print(F("ok\n"));
           resetCommand();
         return;
      } 

      if (input.startsWith("xf:")) {
          input.replace("xf:", "");
          forceFeed = true;
          moveSorterToNextPosition(input.toInt());
          resetCommand();
          FeedScheduled = true;
          IsFeeding = false;
          scheduleRun();
          return;
      }

      if (input.startsWith("getconfig")) {
     
        Serial.print(F("{\"FeedMotorSpeed\":"));
        Serial.print(feedSpeed);

        Serial.print(F(",\"FeedCycleSteps\":"));
        Serial.print(feedSteps);

        Serial.print(F(",\"SortMotorSpeed\":"));
        Serial.print(sortSpeed);

        Serial.print(F(",\"SortSteps\":"));
        Serial.print(sortSteps);

        Serial.print(F(",\"NotificationDelay\":"));
        Serial.print(notificationDelay);

        Serial.print(F(",\"SlotDropDelay\":"));
        Serial.print(slotDropDelay);

        Serial.print(F(",\"AirDropEnabled\":"));
        Serial.print(airDropEnabled);

        Serial.print(F(",\"AirDropPostDelay\":"));
        Serial.print(feedCyclePostDelay);

        Serial.print(F(",\"AirDropPreDelay\":"));
        Serial.print(feedCyclePreDelay);

        Serial.print(F(",\"AirDropSignalTime\":"));
        Serial.print(feedCycleSignalTime);

        Serial.print(F(",\"FeedHomingOffset\":"));
        Serial.print(feedOffsetSteps);
        
         Serial.print(F(",\"SortHomingOffset\":"));
        Serial.print(sortOffsetSteps);

        Serial.print(F(",\"AutoMotorStandbyTimeout\":"));
        Serial.print(autoMotorStandbyTimeout);
        
        Serial.print(F(",\"DebounceTimeout\":"));
        Serial.print(triggerTimeout);

        Serial.print(F(",\"DebouncePauseTime\":"));
        Serial.print(debounceTime);

        #if UseArduinoPWMDimmer == true 
                Serial.print(F(",\"CameraLEDLevel\":"));
                Serial.print(cameraLEDLevel);
        #endif
   
        Serial.print(F("}\n"));
        resetCommand();
        return;      
      }

        if (input.startsWith("debounceTimeout:")) {
          input.replace("debounceTimeout:", "");
          triggerTimeout = input.toInt();
          Serial.print(F("ok\n"));
          resetCommand();
          return;
        }

        if (input.startsWith("debounceTime:")) {
          input.replace("debounceTime:", "");
          debounceTime = input.toInt();
          Serial.print(F("ok\n"));
          resetCommand();
          return;
        }

       //set feed speed. Values 1-100. Def 60
      if (input.startsWith("feedspeed:")) {
        input.replace("feedspeed:", "");
        feedSpeed = input.toInt();
        setFeedMotorSpeed(feedSpeed);
        Serial.print(F("ok\n"));
        resetCommand();
        return;
      }
      //set feed homing offset
      if (input.startsWith("feedhomingoffset:")) {
        input.replace("feedhomingoffset:", "");
        feedOffsetSteps = input.toInt(); //3
        feedHomingOffset = feedOffsetSteps * FEED_MICROSTEPS; //48
        FeedHomingOffsetSteps = feedHomingOffset; //48

        Serial.print(F("ok\n"));
        resetCommand();
        return;
      }

       if (input.startsWith("sorthomingoffset:")) {
        input.replace("sorthomingoffset:", "");
        sortOffsetSteps = input.toInt(); //3
        sortHomingOffset = sortOffsetSteps * SORT_MICROSTEPS; //48
        SortHomingOffsetSteps = sortHomingOffset; //48

        Serial.print(F("ok\n"));
        resetCommand();
        return;
      }

       if (input.startsWith("sortspeed:")) {
        input.replace("sortspeed:", "");
        sortSpeed = input.toInt();
        setSorterMotorSpeed(sortSpeed);
        Serial.print(F("ok\n"));
        resetCommand();
        return;
      }

      //set sort steps. Values 1-100. Def 20
      if (input.startsWith("sortsteps:")) {
        input.replace("sortsteps:", "");
        sortSteps = input.toInt();
        Serial.print(F("ok\n"));
        resetCommand();
        return;
      }

      //set feed steps. Values 1-1000. Def 100
      if (input.startsWith("feedsteps:")) {
        input.replace("feedsteps:", "");
        feedSteps = input.toInt();
        feedMicroSteps = feedSteps * FEED_MICROSTEPS;
        feedOverTravelSteps = feedMicroSteps - (FEED_OVERSTEP_THRESHOLD * FEED_MICROSTEPS);
        Serial.print(F("ok\n"));
        resetCommand();
        return;
      }
      if (input.startsWith("notificationdelay:")) {
        input.replace("notificationdelay:", "");
        notificationDelay = input.toInt();
        Serial.print(F("ok\n"));
        resetCommand();
        return;
      }
      if (input.startsWith("slotdropdelay:")) {
        input.replace("slotdropdelay:", "");
        slotDropDelay = input.toInt();
        dropDelay =  airDropEnabled ? feedCyclePostDelay: slotDropDelay;
        Serial.print(F("ok\n"));
        resetCommand();
        return;
      }
      if (input.startsWith("airdropenabled:")) {
        input.replace("airdropenabled:", "");
        airDropEnabled = stringToBool(input);
        dropDelay =  airDropEnabled ? feedCyclePostDelay: slotDropDelay;
        Serial.print(F("ok\n"));
        resetCommand();
        return;
      }

      if (input.startsWith("airdroppostdelay:")) {
        input.replace("airdroppostdelay:", "");
        feedCyclePostDelay = input.toInt();
        dropDelay =  airDropEnabled ? feedCyclePostDelay: slotDropDelay;
        Serial.print(F("ok\n"));
        resetCommand();
        return;
      }
       if (input.startsWith("airdroppredelay:")) {
        input.replace("airdroppredelay:", "");
        feedCyclePreDelay = input.toInt();
        Serial.print(F("ok\n"));
        resetCommand();
        return;
      }
      if (input.startsWith("airdropdsignalduration:")) {
        input.replace("airdropdsignalduration:", "");
        feedCycleSignalTime = input.toInt();
        Serial.print(F("ok\n"));
        resetCommand();
        return;
      }

      if (input.startsWith("automotorstandbytimeout:")) {
        input.replace("automotorstandbytimeout:", "");
        autoMotorStandbyTimeout = input.toDouble();
        Serial.print(F("ok\n"));
        resetCommand();
        return;
      }
      if (input.startsWith("cameraledlevel:")) {
         input.replace("cameraledlevel:", "");
         adjustCameraLED(input.toInt() );
         //Serial.print(F("LED: "));
         //Serial.print((float)cameraLEDLevel/255.0*100.0);
         //Serial.print(F("%\n"));
         Serial.print(F("ok\n"));
         resetCommand();
         return;
       }

      if (input.startsWith("test:")) {
        input.replace("test:", "");
        IsTestCycle=true;
        testCycleInterval=input.toInt();
        testsCompleted=0;
        FeedScheduled=false;
        FeedCycleInProgress=false;
        Serial.print(F("testing started\n"));
        resetCommand();
        return;
      }

       if (input.startsWith("sorttest:")) {
        input.replace("sorttest:", "");
        IsSortTestCycle=true;
        testCycleInterval=input.toInt();
        testsCompleted=0;
        Serial.print(F("testing started\n"));
        resetCommand();
        return;
      }
     


       if (input.startsWith("ping")) {
        //Serial.print(FreeMem());
        resetCommand();
        Serial.print(F(" ok\n"));
        return;
      }
      resetCommand();
      Serial.print(F("ok\n"));
  }
}

bool stringToBool(String str) {
  str.toLowerCase();
  // Compare the string to "true" and return true if they match
  if(str=="true"){
    return true;
  }
  if(str == "1"){
    return true;
  }
  return false;
  
}

//this method is to run all "other" routines not in the main duty cycles (such as tests)
void runAux(){

  //This runs the feed and sort test if scheduled
  if(IsTestCycle==true&&FeedScheduled==false&&FeedCycleInProgress==false){
    if(testsCompleted<testCycleInterval){
       int slot = random(0,6);
         moveSorterToNextPosition(slot);
        
        FeedScheduled = true;
        IsFeeding = false;
        scheduleRun();
        
        Serial.print(testsCompleted);
        Serial.print(F(" - "));
        Serial.print(slot);
        Serial.print(F("\n"));
        testsCompleted++;

            
    }else{
      IsTestCycle=false;
      testCycleInterval=0;
      testsCompleted=0;
    }
  }

  //this runs the sorter only test cycles if scheduled
  if(IsSortTestCycle==true&&SortInProgress==false){
    if(testsCompleted<testCycleInterval){
       int slot = random(0,8);
       delay(40);
       Serial.print(testsCompleted);
       Serial.print(F(" - Sorting to: "));
       Serial.println(slot);
       moveSorterToPosition(slot);
        testsCompleted++;
    }else{
      moveSorterToPosition(0);
      Serial.println("Sort Test Completed");
      IsSortTestCycle=false;
      testsCompleted=0;
      testCycleInterval=0;
    }
  }
}


void moveSorterToNextPosition(int position){
    sortToSlot=position;
    sortStepsToNextPosition = (qPos1 * sortSteps * SORT_MICROSTEPS) - (qPos2 * sortSteps * SORT_MICROSTEPS);
    sortStepsToNextPositionTracker = sortStepsToNextPosition;
    if(sortStepsToNextPosition !=0){
      theTime = millis();
       slotDelayCalc = (dropDelay - (theTime - timeSinceLastSortMove));
       slotDelayCalc = slotDelayCalc > 0? slotDelayCalc : 1;
       if(slotDelayCalc > dropDelay){
         slotDelayCalc=dropDelay;
       }

      // Serial.println(slotDelayCalc);
      delay(slotDelayCalc);
    }
    qPos1 = qPos2;
    qPos2 =position;
    SortInProgress = true;
    SortComplete = false;
    IsSorting = true;
}

void moveSorterToPosition(int position){
    sortToSlot=position;
    sortStepsToNextPosition = (qPos1 * sortSteps * SORT_MICROSTEPS) - (position * sortSteps * SORT_MICROSTEPS);
    sortStepsToNextPositionTracker = sortStepsToNextPosition;
   
  // Serial.println(position);
   //Serial.println(sortStepsToNextPosition);
    qPos1 =position;
    qPos2 =position;
    SortInProgress = true;
    SortComplete = false;
    IsSorting = true;
}
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

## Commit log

2023-02-12 Reorganized folders and added missing cs7.1 assets
    [CS7.1 9mm Classifier Lid Short.stl, CS7.1 9mm Drop Nozzle.stl, CS7.1 9mm Feed Nozzle - Short.stl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]
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2023-02-24 Create CS7.1 9mm Feed Wheel.stl
    [CS7.1 9mm Feed Wheel.stl]
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2023-02-24 Update CS7.1 Classifier Base.stl
    [CS7.1 Classifier Base.stl]
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2023-02-25 Added additional sorter models
    [CS7.1 Sorter 9-Hole Plate Module.stl, CS7.1 Sorter Base 8 Slot Ramp.stl, CS7.1 Sorter Base.stl]
2023-02-25 added models for light ring
    [CS7.1 Camera Light Ring.stl, CS7.1 Topless Feeder Extension.stl]
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2023-02-25 Added topless feed bracket
    [CS7.1 Topless Feed Bracket.stl, CS7.1 Topless Light Shade.stl]
2023-02-25 Moved assets to folder
    [CS7.1 Topless Feed Bracket.stl, CS7.1 Topless Light Shade.stl]
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2023-02-26 update tension cam shim
    [CS7.1 Classifier Tension Cam Shim M6.stl, CS7.1 Classifier Tension Cam Shim.stl]
2023-02-28 Updated instructions and Sorter pipe
    [CS7.1 Sorter Pipe.stl]
2023-03-02 Added 1in pole base to community
    [Pole_base_v1.stl]
2023-03-02 Fixed error in print size for camera
2023-03-02 Create CS7.1 Sorter Homing Bracket.stl
    [CS7.1 Sorter Homing Bracket.stl]
2023-03-02 Update CS7.1 Sort Pipe Holder.stl
    [CS7.1 Sort Pipe Holder.stl]
2023-03-04 updated arduino for some bugs
    [CS71_Arduino.ino]
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2023-03-06 Update CS7.1 Classifier Lid.stl
    Bug fix.. old lid top was mirrored.
    [CS7.1 Classifier Lid.stl]
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2023-03-08 Update CS7.1 Camera Module.stl
    [CS7.1 Camera Module.stl]
2023-03-08 added prototype mount system, swedish edition
    [CS7.1 Mount - Feed Tube.stl, CS7.1 Mount - Sorter Base.stl, CS7.1 Mount - Universal Pole Mount.stl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]
2023-03-08 updated models - set screw size
    [CS7.1 Classifier Base.stl, CS7.1 Mount - Universal Pole Mount.stl]
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2023-03-08 added enclosures by silverbullit
    [ArduinoBoxRoundedEvenMoreTweaked.stl, ArduinoLidRoundedWCorner-Ears.stl]
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2023-03-09 updated holes from 3.0 to 2.8mm added round tops to avoid supports
    [CS7.1 Sorter Pipe Bracket.stl]
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2023-03-17 Update CS7.1 Electronics Enclosure Small Box.stl
    [CS7.1 Electronics Enclosure Small Box.stl]
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2023-03-18 Added swiss cheeze submarine by silverbullit
    [SCS_4xPins_SwissCheezeSubmarine.stl, SCS_Bottom_wLogo_SwissCheezeSubmarine.stl, SCS_Latch_SwissCheezeSubmarine.stl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]
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2023-03-20 Added new caliber kits for 45 and 308 and some community contributions
    [CS7.1 308Win Drop Nozzle.stl, CS7.1 308Win Feed Nozzle.stl, CS7.1 308Win Feed Wheel.stl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]
2023-03-20 added elec box mount
    [CS7.1 Electronics Box Mount.stl, Thumbscrew_M3.stl]
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2023-03-21 reorged cc and updated arduino code
    [HolyBin.stl, Sorter Bin Tag_Aguila.stl, Sorter Bin Tag_Berdan.stl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]
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2023-03-25 Create CS7.1 Classifier Tension Stop Shim.stl
    [CS7.1 Classifier Tension Stop Shim.stl]
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2023-04-04 Create CS7.1 Caliber Tray.stl
    [CS7.1 Caliber Tray.stl]
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2023-04-12 added 32 sw long caliber conversion
    [CS7.1 32SWLong Feed Nozzle.stl, CS7.1 32SWLong Feed Wheel.stl, CS7.1 Caliber Conversion 32SWLong.stl]
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2023-05-11 Fixed issue where jam in training causes slowness
    [CS71_Arduino.ino]
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2023-11-16 Revert "Update CS71_Arduino.ino"
    This reverts commit a7e5aaab329ed3e99256e97372b016b0f54ee996.
    [CS71_Arduino.ino]
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2024-02-06 Shibby file updates and removal
    All changes done to Shibby related folders. New v2 conversion stuff, new electronics box versions to include microfit.
    [CS7.1 30.06 feed and drop Tubes.stl, CS7.1 38Special tubes.stl, CS7.1 40SW Feed tube.stl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]
2024-02-07 Add files via upload
    Print on side using 4 walls and 40% grid infill. Use M5x6mm heatset inserts in the holes on the upright. Use M5x30mm BHS to adjust the angle of the bowl. This is for the BF556 bowls and mounts.
    [extension_arm.stl]
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2024-02-08 Create Spring Feed Attachments - dillon with rim_(CHRIS_V).stl
    [Spring Feed Attachments - dillon with rim_(CHRIS_V).stl]
2024-02-12 Added the long arm hex sort (LAHS) assets
    [CS7.1 - LAHS - HexPipe - 200mm.stl, CS7.1 - LAHS - Homing Bracket.stl, CS7.1 - LAHS - Pipe Bracket.stl]
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2024-02-17 updated instructions, moved airdrop to new folder, created mods folder
    [AirDrop - Bracket.stl, AirDrop - Nozzle.stl]
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2024-03-11 Added the old style solid brackets to the mount options
    [CS7.1 Offset Bracket - .75s40 - SOLID.stl, CS7.1 Offset Bracket - 1in - SOLID.stl, CS7.1 Pole Mount - .75s40 - SOLID.stl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]
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2024-03-19 fixed int long sleep bug
    [CS71_Arduino.ino]
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2024-08-18 Create CS7.1 - LAHS - HexPipe - 40mm.stl
    [CS7.1 - LAHS - HexPipe - 40mm.stl]
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2024-11-09 Added 50mm hose sorter & 2020 aluminum extrusion mounts
    [2020OffsetMount.step, 2020OffsetTubeMount.step, 2020TubeMount.step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]
2024-11-10 Added lightweight variant for hose sorter saving 60g filament + small improvements
    [Dust Collecter Hose Sorter (Orca Slicer).3mf, Dust Collecter Hose Sorter - Lightweight (Orca Slicer).3mf, Dust Collector Hose Sorter - Lightweight.FCStd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]
2024-11-10 Create CS7.1 Caliber Conversion Kit Tray - for Shibby BF556 Adaptor Drop Tubes.stl
    [CS7.1 Caliber Conversion Kit Tray - for Shibby BF556 Adaptor Drop Tubes.stl]
2024-11-10 Create CS7.1 Box - pwm varient normal box v1.stl
    [CS7.1 Box - pwm varient normal box v1.stl]
2024-11-11 Reduced plate thickness to have more wiggle room for the motor flange
    [Dust Collecter Hose Sorter (Orca Slicer).3mf, Dust Collecter Hose Sorter - Lightweight (Orca Slicer).3mf, Dust Collector Hose Sorter - Lightweight.FCStd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]
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2024-11-13 Move enclosure mount to correct directory
    [Electronics Enclosure Mount 2020 Extrusion.step]
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2024-11-13 fixed power button dia
    [Spacious Electronics Enclosure - Software Dimmer - Dual Fan.step, Spacious Electronics Enclosure.FCStd]
2024-11-13 Create CS7.1- Dimmer Hole Plug for PWM conversion.stl
    2pc plug and cap for plugging mechanical dimmer hole when converting to software controlled dimmer
    [CS7.1- Dimmer Hole Plug for PWM conversion.stl]
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2025-05-29 fixed bug in forcefeed
    [CS71_Arduino.ino]
2025-05-31 fixed bug in feed for disabled feed sensor
    [CS71_Arduino.ino]
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
